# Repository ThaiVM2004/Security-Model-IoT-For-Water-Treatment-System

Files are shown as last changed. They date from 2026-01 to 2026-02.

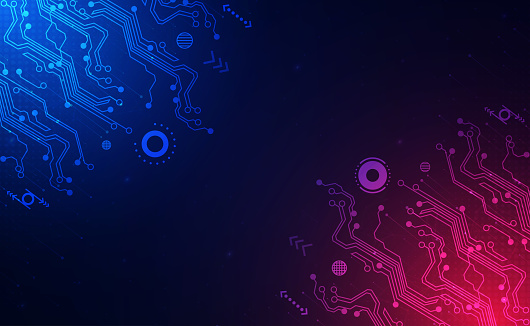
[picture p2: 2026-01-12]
Source/Web Code/superviso-ui/src/Components/Assets/background-4.jpg

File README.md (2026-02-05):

# BUILD A SECURITY MODEL IOT FOR WATER TREATMENT SYSTEM

In this project, I want to build a security model iot, it is applicated in water treatment system.

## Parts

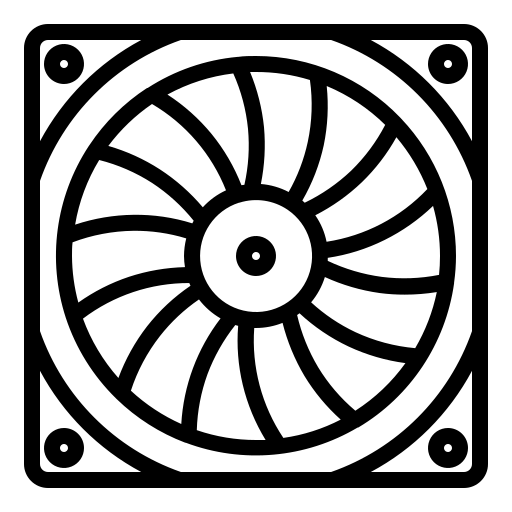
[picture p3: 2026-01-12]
Source/Web Code/superviso-ui/src/Components/Assets/fan-industrial.png

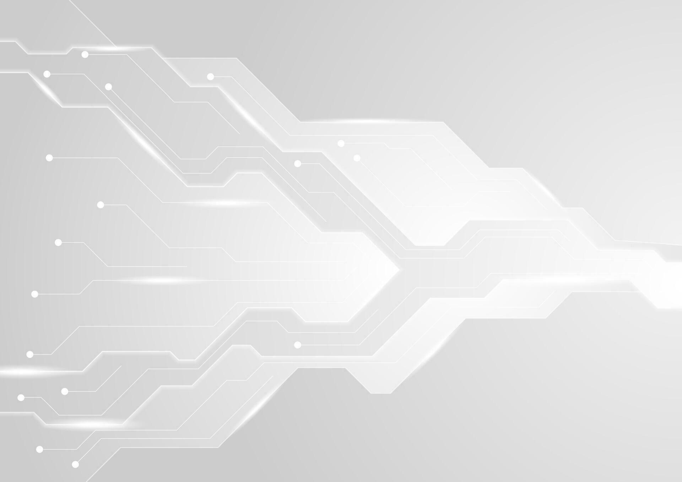
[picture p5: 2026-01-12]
Source/Web Code/superviso-ui/src/Components/Assets/background-3.jpg

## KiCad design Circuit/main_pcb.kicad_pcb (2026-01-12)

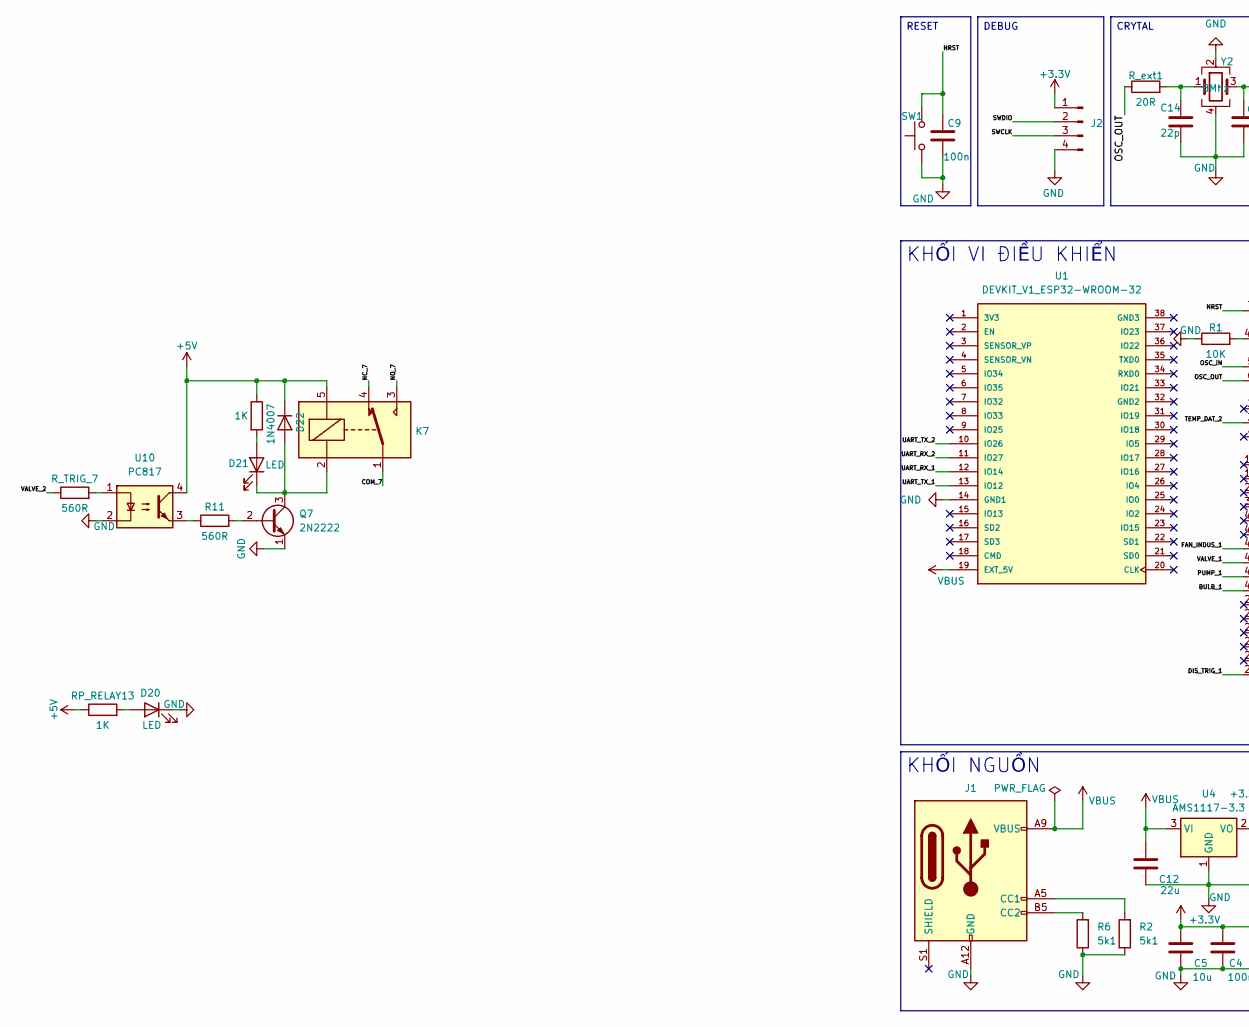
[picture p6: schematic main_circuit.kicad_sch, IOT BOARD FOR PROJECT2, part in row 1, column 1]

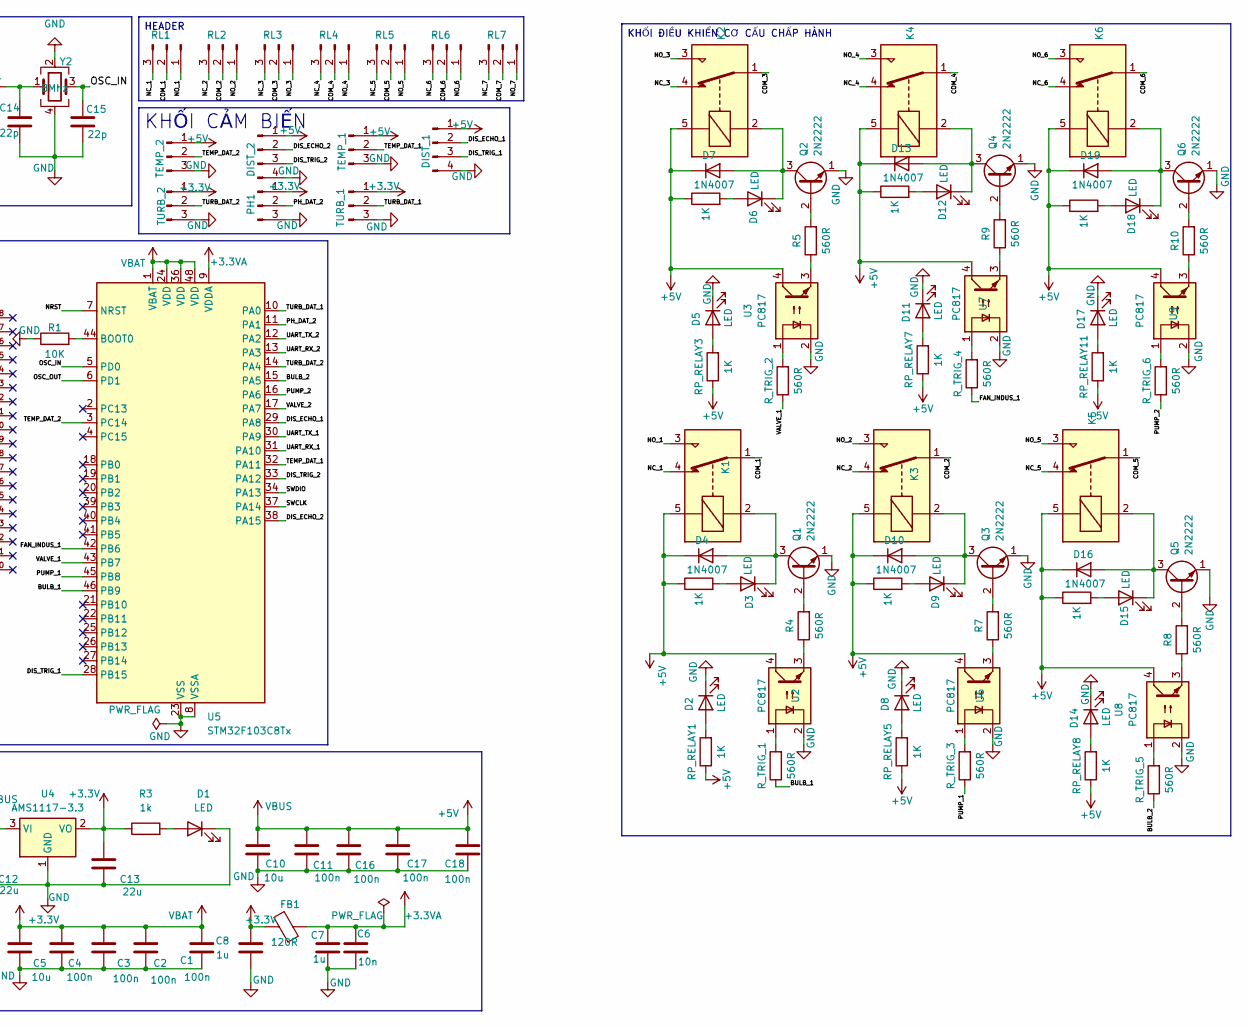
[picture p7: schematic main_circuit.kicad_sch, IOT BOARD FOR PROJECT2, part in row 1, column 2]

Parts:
C1, C2, C3, C4, C9, C11, C16, C17, C18: 100n; C_0805_2012Metric
C5, C10: 10u; C_0805_2012Metric
C6: 10n; C_0805_2012Metric
C7, C8: 1u; C_0805_2012Metric
C12, C13: 22u; C_0805_2012Metric
C14, C15: 22p; C_0603_1608Metric
D1, D2, D3, D5, D6, D8, D9, D11, D12, D14, D15, D17, D18, D20, D21: LED; LED_0805_2012Metric
D4, D7, D10, D13, D16, D19, D22: 1N4007; D_DO-41_SOD81_P10.16mm_Horizontal
DIST_1, DIST_2: Conn_01x04_Pin; PinHeader_1x04_P2.54mm_Vertical
FB1: 120R; L_0805_2012Metric
J1: USB_C_Receptacle_PowerOnly_6P; USB_C_Receptacle_GCT_USB4125-xx-x_6P_TopMnt_Horizontal
J2: ST-LINK; PinHeader_1x04_P2.54mm_Vertical
K1, K2, K3, K4, K5, K6, K7: SANYOU_SRD_Form_C; Relay_SPDT_SANYOU_SRD_Series_Form_C
PH1: Conn_01x03_Pin; PinHeader_1x03_P2.54mm_Vertical
Q1, Q2, Q3, Q4, Q5, Q6, Q7: 2N2222; PinHeader_1x03_P1.27mm_Vertical
R1: 10K; R_0805_2012Metric
R2, R6: 5k1; R_0805_2012Metric
R3: 1k; R_0805_2012Metric
R4, R5, R7, R8, R9, R10, R11: 560R; R_0805_2012Metric
RL1, RL2, RL3, RL4, RL5, RL6, RL7: Conn_01x03_Pin; PinHeader_1x03_P2.54mm_Vertical
RP_RELAY1, RP_RELAY2, RP_RELAY3, RP_RELAY4, RP_RELAY5, RP_RELAY6, RP_RELAY7, RP_RELAY8, RP_RELAY9, RP_RELAY10, RP_RELAY11, RP_RELAY12, RP_RELAY13, RP_RELAY14: 1K; R_0805_2012Metric
R_TRIG_1, R_TRIG_2, R_TRIG_3, R_TRIG_4, R_TRIG_5, R_TRIG_6, R_TRIG_7: 560R; R_0805_2012Metric
R_ext1: 20R; R_0805_2012Metric
SW1: SW_Push; SW_SPST_PTS647_Sx70
TEMP_1, TEMP_2: Conn_01x03_Pin; PinHeader_1x03_P2.54mm_Vertical
TURB_1, TURB_2: Conn_01x03_Pin; PinHeader_1x03_P2.54mm_Vertical
U1: DEVKIT_V1_ESP32-WROOM-32; MODULE_DEVKIT_V1_ESP32-WROOM-32; PARTREV N/A
U2, U3, U6, U7, U8, U9, U10: PC817; DIP-4_W7.62mm
U4: AMS1117-3.3; SOT-223-3_TabPin2
U5: STM32F103C8Tx; LQFP-48_7x7mm_P0.5mm
Y2: 8Mhz; Crystal_SMD_5032-4Pin_5.0x3.2mm

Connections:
+3.3V: C1.1, C2.1, C3.1, C4.1, C5.1, C8.1, C13.1, FB1.2, J2.1, PH1.1, R3.1, TURB_1.1, TURB_2.1, U4.2 (VO), U5.1 (VBAT), U5.24 (VDD), U5.36 (VDD), U5.48 (VDD)
+3.3VA: C6.1, C7.1, FB1.1, U5.9 (VDDA)
+5V: C10.1, C11.1, C12.1, C16.1, C17.1, C18.1, D4.1 (K), D7.1 (K), D10.1 (K), D13.1 (K), D16.1 (K), D19.1 (K), D22.1 (K), DIST_1.1, DIST_2.1, J1.A9 (VBUS), J1.B9 (VBUS), K1.5, K2.5, K3.5, K4.5, K5.5, K6.5, K7.5, RP_RELAY1.1, RP_RELAY2.1, RP_RELAY3.1, RP_RELAY4.1, RP_RELAY5.1, RP_RELAY6.1, RP_RELAY7.1, RP_RELAY8.1, RP_RELAY9.1, RP_RELAY10.1, RP_RELAY11.1, RP_RELAY12.1, RP_RELAY13.1, RP_RELAY14.1, TEMP_1.1, TEMP_2.1, U1.19 (EXT_5V), U2.4, U3.4, U4.3 (VI), U6.4, U7.4, U8.4, U9.4, U10.4
/BULB_1: R_TRIG_1.1, U5.46 (PB9)
/BULB_2: R_TRIG_5.1, U5.15 (PA5)
/COM_1: K1.1, RL1.2
/COM_2: K3.1, RL2.2
/COM_3: K2.1, RL3.2
/COM_4: K4.1, RL4.2
/COM_5: K5.1, RL5.2
/COM_6: K6.1, RL6.2
/COM_7: K7.1, RL7.2
/DIS_ECHO_1: DIST_1.2, U5.29 (PA8)
/DIS_ECHO_2: DIST_2.2, U5.38 (PA15)
/DIS_TRIG_1: DIST_1.3, U5.28 (PB15)
/DIS_TRIG_2: DIST_2.3, U5.33 (PA12)
/FAN_INDUS_1: R_TRIG_4.1, U5.42 (PB6)
/NC_1: K1.4, RL1.3
/NC_2: K3.4, RL2.3
/NC_3: K2.4, RL3.3
/NC_4: K4.4, RL4.3
/NC_5: K5.4, RL5.3
/NC_6: K6.4, RL6.3
/NC_7: K7.4, RL7.3
/NO_1: K1.3, RL1.1
/NO_2: K3.3, RL2.1
/NO_3: K2.3, RL3.1
/NO_4: K4.3, RL4.1
/NO_5: K5.3, RL5.1
/NO_6: K6.3, RL6.1
/NO_7: K7.3, RL7.1
/NRST: C9.1, SW1.2, U5.7 (NRST)
/OSC_IN: C15.1, U5.5 (PD0), Y2.3
/OSC_OUT: R_ext1.1, U5.6 (PD1)
/PH_DAT_2: PH1.2, U5.11 (PA1)
/PUMP_1: R_TRIG_3.1, U5.45 (PB8)
/PUMP_2: R_TRIG_6.1, U5.16 (PA6)
/SWCLK: J2.3, U5.37 (PA14)
/SWDIO: J2.2, U5.34 (PA13)
/TEMP_DAT_1: TEMP_1.2, U5.32 (PA11)
/TEMP_DAT_2: TEMP_2.2, U5.3 (PC14)
/TURB_DAT_1: TURB_1.2, U5.10 (PA0)
/TURB_DAT_2: TURB_2.2, U5.14 (PA4)
/UART_RX_1: U1.12 (IO14), U5.31 (PA10)
/UART_RX_2: U1.11 (IO27), U5.13 (PA3)
/UART_TX_1: U1.13 (IO12), U5.30 (PA9)
/UART_TX_2: U1.10 (IO26), U5.12 (PA2)
/VALVE_1: R_TRIG_2.1, U5.43 (PB7)
/VALVE_2: R_TRIG_7.1, U5.17 (PA7)
GND: C1.2, C2.2, C3.2, C4.2, C5.2, C6.2, C7.2, C8.2, C9.2, C10.2, C11.2, C12.2, C13.2, C14.2, C15.2, C16.2, C17.2, C18.2, D1.1 (K), D2.1 (K), D5.1 (K), D8.1 (K), D11.1 (K), D14.1 (K), D17.1 (K), D20.1 (K), DIST_1.4, DIST_2.4, J1.A12 (GND), J1.B12 (GND), J2.4, PH1.3, Q1.1 (E), Q2.1 (E), Q3.1 (E), Q4.1 (E), Q5.1 (E), Q6.1 (E), Q7.1 (E), R1.1, R2.1, R6.1, SW1.1, TEMP_1.3, TEMP_2.3, TURB_1.3, TURB_2.3, U1.14 (GND1), U2.2, U3.2, U4.1 (GND), U5.8 (VSSA), U5.23 (VSS), U5.35 (VSS), U5.47 (VSS), U6.2, U7.2, U8.2, U9.2, U10.2, Y2.2, Y2.4
unnamed: C14.1, R_ext1.2, Y2.1
unnamed: D1.2 (A), R3.2
unnamed: D2.2 (A), RP_RELAY1.2
unnamed: D3.2 (A), RP_RELAY2.2
unnamed: D3.1 (K), D4.2 (A), K1.2, Q1.3 (C)
unnamed: D5.2 (A), RP_RELAY3.2
unnamed: D6.2 (A), RP_RELAY4.2
unnamed: D6.1 (K), D7.2 (A), K2.2, Q2.3 (C)
unnamed: D8.2 (A), RP_RELAY5.2
unnamed: D9.2 (A), RP_RELAY6.2
unnamed: D9.1 (K), D10.2 (A), K3.2, Q3.3 (C)
unnamed: D11.2 (A), RP_RELAY7.2
unnamed: D12.2 (A), RP_RELAY10.2
unnamed: D12.1 (K), D13.2 (A), K4.2, Q4.3 (C)
unnamed: D14.2 (A), RP_RELAY8.2
unnamed: D15.2 (A), RP_RELAY9.2
unnamed: D15.1 (K), D16.2 (A), K5.2, Q5.3 (C)
unnamed: D17.2 (A), RP_RELAY11.2
unnamed: D18.2 (A), RP_RELAY12.2
unnamed: D18.1 (K), D19.2 (A), K6.2, Q6.3 (C)
unnamed: D20.2 (A), RP_RELAY13.2
unnamed: D21.2 (A), RP_RELAY14.2
unnamed: D21.1 (K), D22.2 (A), K7.2, Q7.3 (C)
unnamed: J1.A5 (CC1), R2.2
unnamed: J1.B5 (CC2), R6.2
unnamed: Q1.2 (B), R4.2
unnamed: Q2.2 (B), R5.2
unnamed: Q3.2 (B), R7.2
unnamed: Q4.2 (B), R9.2
unnamed: Q5.2 (B), R8.2
unnamed: Q6.2 (B), R10.2
unnamed: Q7.2 (B), R11.2
unnamed: R4.1, U2.3
unnamed: R5.1, U3.3
unnamed: R7.1, U6.3
unnamed: R8.1, U8.3
unnamed: R9.1, U7.3
unnamed: R10.1, U9.3
unnamed: R11.1, U10.3
unnamed: R_TRIG_1.2, U2.1
unnamed: R_TRIG_2.2, U3.1
unnamed: R_TRIG_3.2, U6.1
unnamed: R_TRIG_4.2, U7.1
unnamed: R_TRIG_5.2, U8.1
unnamed: R_TRIG_6.2, U9.1
unnamed: R_TRIG_7.2, U10.1
unnamed: R1.2, U5.44 (BOOT0)

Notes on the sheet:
KHỐI ĐIỀU KHIỂN CƠ CẤU CHẤP HÀNH
KHỐI CẢM BIẾN
DEBUG
HEADER
KHỐI NGUỒN
CRYTAL
KHỐI VI ĐIỀU KHIỂN
RESET

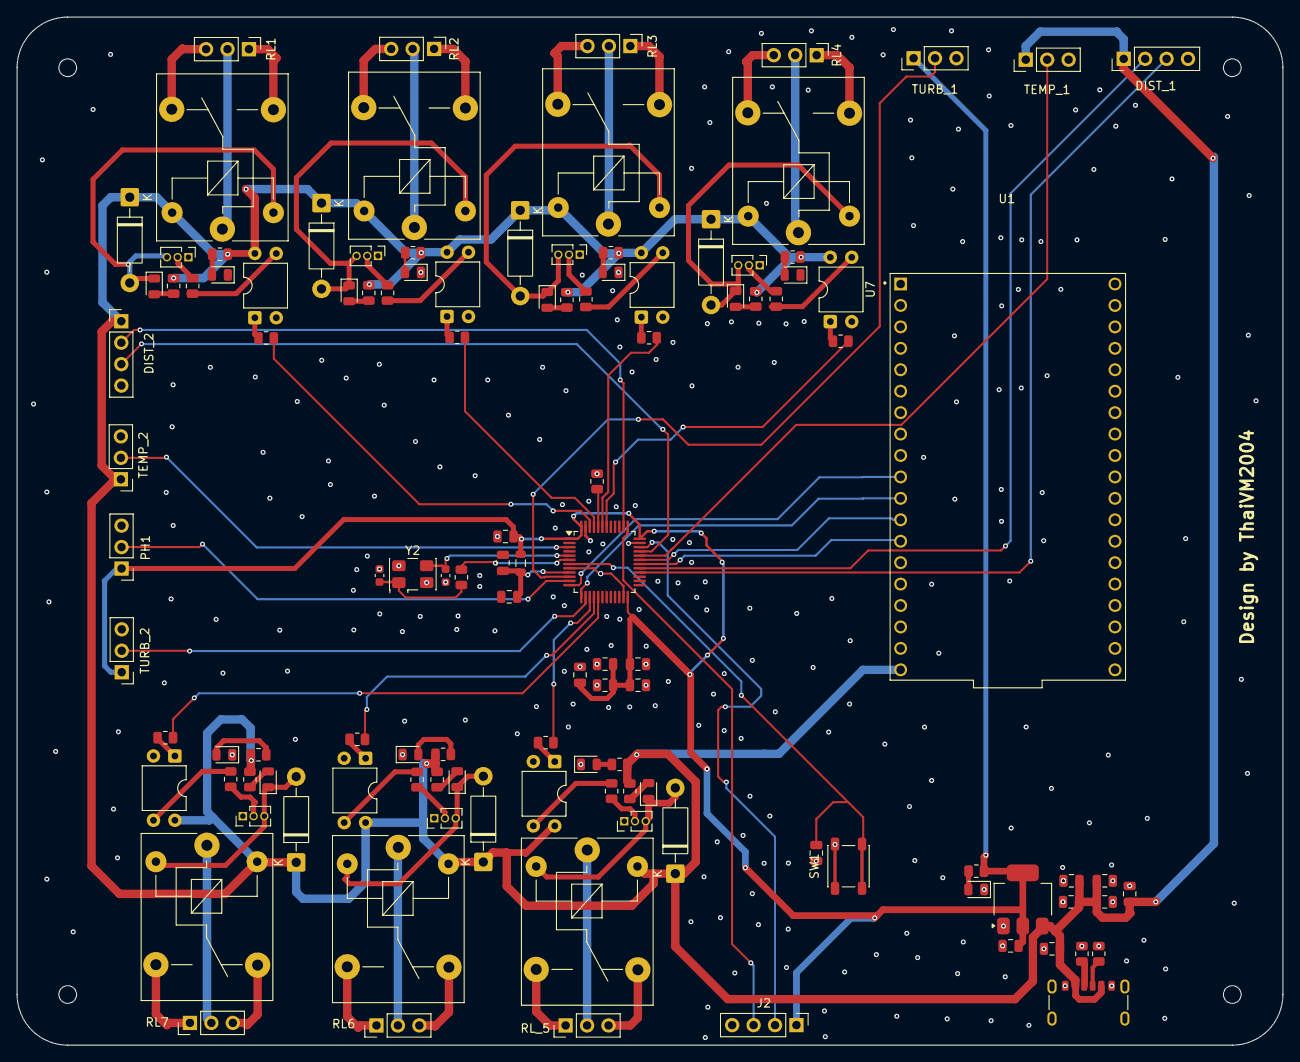
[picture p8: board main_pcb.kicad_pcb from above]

Board: 2 copper layers, 150.0 x 121.8 mm, 120 parts (0 on the bottom side), 97 nets.

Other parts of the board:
H1, H2, H3, H4: MountingHole; MountingHole_2.1mm

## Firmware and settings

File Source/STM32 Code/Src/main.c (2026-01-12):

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
/* Includes ------------------------------------------------------------------*/
#include "main.h"
#include "cmsis_os.h"

/* USER CODE BEGIN Includes */

#include "string.h"
#include "stdio.h"
#include "temp_delay.h"
#include "water_level.h"
#include "turbidity.h"
#include "pH.h"

/* USER CODE END Includes */

/* USER CODE BEGIN PD */

osThreadId_t sensorTask_1_Handle;
osThreadId_t sensorTask_2_Handle;


osMutexId_t uartMutexHandle;
const osMutexAttr_t uartMutex_attributes = {
    .name = "uartMutex"
};

osMutexId_t tempMutex;
osMutexId_t adcMutex;




void StartUartRxTask(void *arg);
void StartSensorTask_1(void *arg);
void StartSensorTask_2(void *arg);

TempSensor_t tempSensor_1;
TempSensor_t tempSensor_2;

HCSR04_t hcsr04_1;
HCSR04_t hcsr04_2;

Turbidity_t turb1;
Turbidity_t turb2;


#define UART_LINE_MAX 64
static uint8_t esp_rx_byte;
static char uart_line_buffer[UART_LINE_MAX];
static uint16_t uart_line_idx = 0;


/* USER CODE END PD */

ADC_HandleTypeDef hadc1;

TIM_HandleTypeDef htim1;
TIM_HandleTypeDef htim2;
TIM_HandleTypeDef htim4;

UART_HandleTypeDef huart1;
UART_HandleTypeDef huart2;

/* Definitions for defaultTask */
osThreadId_t defaultTaskHandle;
const osThreadAttr_t defaultTask_attributes = {
  .name = "defaultTask",
  .stack_size = 128 * 4,
  .priority = (osPriority_t) osPriorityNormal,
};
void SystemClock_Config(void);
static void MX_GPIO_Init(void);
static void MX_USART2_UART_Init(void);
static void MX_TIM1_Init(void);
static void MX_ADC1_Init(void);
static void MX_USART1_UART_Init(void);
static void MX_TIM4_Init(void);
static void MX_TIM2_Init(void);
void StartDefaultTask(void *argument);

/* USER CODE BEGIN 0 */
void HAL_TIM_IC_CaptureCallback(TIM_HandleTypeDef *htim)
{
    if (htim->Instance == TIM1)
    {
        HCSR04_TIM_IC_Callback(&hcsr04_1, htim);
    }
    else if (htim->Instance == TIM2)
    {
        HCSR04_TIM_IC_Callback(&hcsr04_2, htim);
    }
}
void control_device(const char *name, uint8_t state)
{
    GPIO_PinState pinState = (state ? GPIO_PIN_SET : GPIO_PIN_RESET);

    if (strcmp(name, "bulb1") == 0)
        HAL_GPIO_WritePin(GPIOB, GPIO_PIN_9, pinState);

    else if (strcmp(name, "pump1") == 0)
        HAL_GPIO_WritePin(GPIOB, GPIO_PIN_8, pinState);

    else if (strcmp(name, "valve1") == 0)
        HAL_GPIO_WritePin(GPIOB, GPIO_PIN_7, pinState);
    else if (strcmp(name, "fan_industrial1") == 0)
        HAL_GPIO_WritePin(GPIOB, GPIO_PIN_6, pinState);
    else if (strcmp(name, "bulb2") == 0)
        HAL_GPIO_WritePin(GPIOA, GPIO_PIN_5, pinState);
    else if (strcmp(name, "pump2") == 0)
        HAL_GPIO_WritePin(GPIOA, GPIO_PIN_6, pinState);
    else if (strcmp(name, "valve2") == 0)
        HAL_GPIO_WritePin(GPIOA, GPIO_PIN_7, pinState);
    else if (strcmp(name, "fan_industrial2") == 0)
        HAL_GPIO_WritePin(GPIOB, GPIO_PIN_0, pinState);

    else
        return;
}

void StartSensorTask_1(void *arg)

{




    for (;;)
    {
    	HCSR04_Trigger(&hcsr04_1);
        HAL_GPIO_TogglePin(GPIOC, GPIO_PIN_13);

        // Đọc nhiệt độ với mutex
        osMutexAcquire(tempMutex, osWaitForever);
        float temp1 = Temp_Read(&tempSensor_1);
        osMutexRelease(tempMutex);

        // Đọc water level
        uint32_t water = HCSR04_GetDistance(&hcsr04_1);

        // Đọc TDS với mutex
        osMutexAcquire(adcMutex, osWaitForever);
        float tds = TURBIDITY_Read(&turb1);
        osMutexRelease(adcMutex);

        // Gửi UART
        char msg[128];
        int len = snprintf(msg, sizeof(msg),
                           "SENSOR1:TEMP:%.2f;WATER:%lu;TDS:%.2f;PH:%.2f\r\n",
                           temp1, water, tds, 0.0f);

        osMutexAcquire(uartMutexHandle, osWaitForever);
        HAL_UART_Transmit(&huart1, (uint8_t *)msg, len, 1000);
        osMutexRelease(uartMutexHandle);

//        HCSR04_Trigger(&hcsr04_1);
        osDelay(2000);
    }
}

void StartSensorTask_2(void *arg)
{


    for (;;)
    {
        HCSR04_Trigger(&hcsr04_2);
        osMutexAcquire(tempMutex, osWaitForever);
        float temp2 = Temp_Read(&tempSensor_2);
        osMutexRelease(tempMutex);

        // Đọc water level
        uint32_t water2 = HCSR04_GetDistance(&hcsr04_2);

        // Đọc TDS và pH với mutex
        osMutexAcquire(adcMutex, osWaitForever);
        float tds2 = TURBIDITY_Read(&turb2)*10;
        float ph = PH_ReadValue();
        osMutexRelease(adcMutex);

        // Gửi UART
        char msg[128];
        int len = snprintf(msg, sizeof(msg),
                           "SENSOR2:TEMP:%.2f;WATER:%lu;TDS:%.2f;PH:%.2f\r\n",
                           temp2, water2, tds2, ph);

        osMutexAcquire(uartMutexHandle, osWaitForever);
        HAL_UART_Transmit(&huart1, (uint8_t *)msg, len, 1000);
        osMutexRelease(uartMutexHandle);

//        HCSR04_Trigger(&hcsr04_2);
        osDelay(2000);
    }
}


void process_uart2_cmd(char *line)
{
    if (line == NULL) return;

    /* command expected: device/action   e.g. pump1/on or pump1/off */
    char *device = strtok(line, "/");
    char *action = strtok(NULL, "/");

    if (!device || !action) return;

    if (strcmp(action, "on") == 0)
        control_device(device, 1);
    else
        control_device(device, 0);

}

void HAL_UART_RxCpltCallback(UART_HandleTypeDef *huart)
{
    if (huart->Instance == USART2)
    {
        char c = (char)esp_rx_byte;

        if (c != '\n' && c != '\r')
        {
            uart_line_buffer[uart_line_idx++] = c;
            if (uart_line_idx >= UART_LINE_MAX)
                uart_line_idx = 0;
        }
        else
        {
            uart_line_buffer[uart_line_idx] = '\0';

            process_uart2_cmd(uart_line_buffer);

            uart_line_idx = 0;
        }

        HAL_UART_Receive_IT(&huart2, &esp_rx_byte, 1);
    }
}
/* USER CODE END 0 */

/**
  * @brief  The application entry point.
  * @retval int
  */
int main(void)
{

  /* MCU Configuration--------------------------------------------------------*/

  /* Reset of all peripherals, Initializes the Flash interface and the Systick. */
  HAL_Init();

  /* Configure the system clock */
  SystemClock_Config();

  /* Initialize all configured peripherals */
  MX_GPIO_Init();
  MX_USART2_UART_Init();
  MX_TIM1_Init();
  MX_ADC1_Init();
  MX_USART1_UART_Init();
  MX_TIM4_Init();
  MX_TIM2_Init();
  /* USER CODE BEGIN 2 */
  //INIT FUNCTION
  //Cam bien muc nuoc
  HCSR04_Init(&hcsr04_1, &htim1, TIM_CHANNEL_1, GPIOB, GPIO_PIN_15);
  HCSR04_Init(&hcsr04_2, &htim2, TIM_CHANNEL_1, GPIOA, GPIO_PIN_12);
  //Dieu khien GPIO
  HAL_UART_Receive_IT(&huart2, &esp_rx_byte, 1);
  //Ngat de do xung cam bien muc nuoc
  HAL_TIM_IC_Start_IT(&htim1, TIM_CHANNEL_1);
  HAL_TIM_IC_Start_IT(&htim2, TIM_CHANNEL_1);
  //Cam bien nhiet do
  HAL_TIM_Base_Start(&htim4);
  Temp_Init(&tempSensor_1, &htim4, GPIOA, GPIO_PIN_11);
  Temp_Init(&tempSensor_2, &htim4, GPIOC, GPIO_PIN_14);
  //Cam bien pH
  PH_AttachADC(&hadc1, ADC_CHANNEL_1);
  PH_InitFromTwoPoints(0.392f, 2.5f,
		  	  	  	  1.54f, 10.5f);
  //Cam bien do duc
  TURBIDITY_Init(&turb1, &hadc1, ADC_CHANNEL_0);  // sensor 1
  TURBIDITY_Init(&turb2, &hadc1, ADC_CHANNEL_4);  // sensor 2



  /* USER CODE END 2 */

  /* Init scheduler */
  osKernelInitialize();

  /* USER CODE BEGIN RTOS_MUTEX */
  /* add mutexes, ... */
  uartMutexHandle = osMutexNew(&uartMutex_attributes);
  const osMutexAttr_t adcMutex_attr = { .name = "adcMutex" };
  const osMutexAttr_t tempMutex_attr = { .name = "tempMutex" };
  adcMutex = osMutexNew(&adcMutex_attr);
  tempMutex = osMutexNew(&tempMutex_attr);

  if (uartMutexHandle == NULL || adcMutex == NULL || tempMutex == NULL)
  {
      Error_Handler();
  }
  /* USER CODE END RTOS_MUTEX */

  /* USER CODE BEGIN RTOS_SEMAPHORES */
  /* add semaphores, ... */
  /* USER CODE END RTOS_SEMAPHORES */

  /* USER CODE BEGIN RTOS_TIMERS */
  /* start timers, add new ones, ... */
  /* USER CODE END RTOS_TIMERS */

  /* USER CODE BEGIN RTOS_QUEUES */
  /* add queues, ... */
  /* USER CODE END RTOS_QUEUES */

  /* Create the thread(s) */
  /* creation of defaultTask */
  defaultTaskHandle = osThreadNew(StartDefaultTask, NULL, &defaultTask_attributes);

  /* USER CODE BEGIN RTOS_THREADS */
  /* add threads, ... */


  const osThreadAttr_t sensor_1_Attr = {
      .name = "SENSOR_1",
      .priority = osPriorityHigh,
      .stack_size = 2048
  };
  const osThreadAttr_t sensor_2_Attr = {
      .name = "SENSOR_2",
      .priority = osPriorityNormal,
      .stack_size = 2048
  };


   sensorTask_1_Handle = osThreadNew(StartSensorTask_1, NULL, &sensor_1_Attr);
   sensorTask_2_Handle = osThreadNew(StartSensorTask_2, NULL, &sensor_2_Attr);





//  uartRxTaskHandle = osThreadNew(StartUartRxTask, NULL, &uartAttr);

  /* USER CODE END RTOS_THREADS */

  /* USER CODE BEGIN RTOS_EVENTS */
  /* add events, ... */
  /* USER CODE END RTOS_EVENTS */

  /* Start scheduler */
  osKernelStart();

  /* We should never get here as control is now taken by the scheduler */

  /* Infinite loop */
  /* USER CODE BEGIN WHILE */
  while (1)
  {
    /* USER CODE END WHILE */

    /* USER CODE BEGIN 3 */
  }
  /* USER CODE END 3 */
}

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
/* USER CODE BEGIN Header_StartDefaultTask */
/**
  * @brief  Function implementing the defaultTask thread.
  * @param  argument: Not used
  * @retval None
  */
/* USER CODE END Header_StartDefaultTask */
void StartDefaultTask(void *argument)
{
  /* USER CODE BEGIN 5 */
  /* Infinite loop */
  for(;;)
  {
    osDelay(1);
  }
  /* USER CODE END 5 */
}

/**
  * @brief  This function is executed in case of error occurrence.
  * @retval None
  */
void Error_Handler(void)
{
  /* USER CODE BEGIN Error_Handler_Debug */
  /* User can add his own implementation to report the HAL error return state */
  __disable_irq();
  while (1)
  {
  }
  /* USER CODE END Error_Handler_Debug */
}

#ifdef  USE_FULL_ASSERT
/**
  * @brief  Reports the name of the source file and the source line number
  *         where the assert_param error has occurred.
  * @param  file: pointer to the source file name
  * @param  line: assert_param error line source number
  * @retval None
  */
void assert_failed(uint8_t *file, uint32_t line)
{
  /* USER CODE BEGIN 6 */
  /* User can add his own implementation to report the file name and line number,
     ex: printf("Wrong parameters value: file %s on line %d\r\n", file, line) */
  /* USER CODE END 6 */
}
#endif /* USE_FULL_ASSERT */

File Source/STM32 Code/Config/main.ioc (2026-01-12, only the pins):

Mcu.UserName=STM32F103C8Tx
PA0-WKUP.Signal=ADCx_IN0
PA1.Signal=ADCx_IN1
PA10.Signal=USART1_RX
PA11.Signal=GPIO_Output
PA12.Signal=GPIO_Output
PA15.Signal=S_TIM2_CH1_ETR
PA2.Signal=USART2_TX
PA3.Signal=USART2_RX
PA4.Signal=ADCx_IN4
PA5.Signal=GPIO_Output
PA6.Signal=GPIO_Output
PA7.Signal=GPIO_Output
PA8.Signal=S_TIM1_CH1
PA9.Signal=USART1_TX
PB0.Signal=GPIO_Output
PB15.Signal=GPIO_Output
PB6.Signal=GPIO_Output
PB7.Signal=GPIO_Output
PB8.Signal=GPIO_Output
PB9.Signal=GPIO_Output
PC13-TAMPER-RTC.Signal=GPIO_Output
PC14-OSC32_IN.Signal=GPIO_Output
PD0-OSC_IN.Signal=RCC_OSC_IN
PD1-OSC_OUT.Signal=RCC_OSC_OUT

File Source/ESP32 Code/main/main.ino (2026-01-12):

#include <WiFi.h>
#include <PubSubClient.h>
#include <ArduinoJson.h>


const char* ssid = "HOBAHOME TRET2";
const char* password = "12345678";
const char* mqtt_server = "192.168.1.115";
const int   mqtt_port  = 1883;

const char* mqtt_sub_topic   = "iot/control";
const char* mqtt_pub_sensor1 = "iot/sensor1";
const char* mqtt_pub_sensor2 = "iot/sensor2";

WiFiClient espClient;
PubSubClient client(espClient);


HardwareSerial UART_CMD(2);

HardwareSerial UART_SENSOR(1);

String uartSensorBuffer = "";

int mapWaterLevel(int distanceCm)
{

    
    const int EMPTY_DISTANCE = 12.5;  
    const int FULL_DISTANCE  = 1;   
    

    if (distanceCm >= EMPTY_DISTANCE) return 0;
    if (distanceCm <= FULL_DISTANCE)  return 100;
    
    int percentage = map(distanceCm, EMPTY_DISTANCE, FULL_DISTANCE, 0, 100);
    
    if (percentage < 0)   percentage = 0;
    if (percentage > 100) percentage = 100;
    
    return percentage;
}

void callback(char* topic, byte* payload, unsigned int length)
{
    StaticJsonDocument<256> doc;
    if (deserializeJson(doc, payload, length)) return;

    const char* device = doc["device"];
    const char* action = doc["action"];
    if (!device || !action) return;

    char cmd[64];
    snprintf(cmd, sizeof(cmd), "%s/%s\n", device, action);

    Serial.print("TX → STM32 (UART2): ");
    Serial.print(cmd);

    UART_CMD.print(cmd);
}

void reconnect()
{
    while (!client.connected())
    {
        Serial.print("MQTT connecting... ");

        if (client.connect("ESP32-UART-HUB"))
        {
            Serial.println("OK");
            client.subscribe(mqtt_sub_topic);
        }
        else
        {
            Serial.print("Failed, rc=");
            Serial.println(client.state());
            delay(2000);
        }
    }
}

void publishSensorData(String raw)
{
    StaticJsonDocument<256> doc;

    if (raw.startsWith("SENSOR1:"))
    {
        float temp = 0;
        int   waterRaw = 0;  
        float tds  = 0;

        int t1 = raw.indexOf("TEMP:");
        int t2 = raw.indexOf(";WATER:");
        int t3 = raw.indexOf(";TDS:");

        if (t1 < 0 || t2 < 0 || t3 < 0) return;

        temp     = raw.substring(t1 + 5, t2).toFloat();
        waterRaw = raw.substring(t2 + 7, t3).toInt();
        tds      = raw.substring(t3 + 5).toFloat();

  
        int waterPercent = mapWaterLevel(waterRaw);

        doc["temp"]  = temp;
        doc["water"] = waterPercent;  
        doc["tds"]   = tds;

        char jsonOut[128];
        serializeJson(doc, jsonOut);

        Serial.print("MQTT publish → SENSOR1:");
        Serial.println(jsonOut);

        client.publish(mqtt_pub_sensor1, jsonOut);
        return;
    }

    if (raw.startsWith("SENSOR2:"))
    {
        float temp = 0;
        int   waterRaw = 0;  
        float tds  = 0;
        float ph   = 0;

        int t1 = raw.indexOf("TEMP:");
        int t2 = raw.indexOf(";WATER:");
        int t3 = raw.indexOf(";TDS:");
        int t4 = raw.indexOf(";PH:");

        if (t1 < 0 || t2 < 0 || t3 < 0 || t4 < 0) return;

        temp     = raw.substring(t1 + 5, t2).toFloat();
        waterRaw = raw.substring(t2 + 7, t3).toInt();
        tds      = raw.substring(t3 + 5, t4).toFloat();
        ph       = raw.substring(t4 + 4).toFloat();


        int waterPercent = mapWaterLevel(waterRaw);

        doc["temp"]  = temp;
        doc["water"] = waterPercent;  
        doc["tds"]   = tds;
        doc["ph"]    = ph;

        char jsonOut[128];
        serializeJson(doc, jsonOut);

        Serial.print("MQTT publish → SENSOR2:");
        Serial.println(jsonOut);

        client.publish(mqtt_pub_sensor2, jsonOut);
        return;
    }
}


void setup()
{
    Serial.begin(115200);

    
    UART_CMD.begin(115200, SERIAL_8N1, 26, 27); 
    Serial.println("UART2 Ready (Commands → STM32)");

   
    UART_SENSOR.begin(9600, SERIAL_8N1, 12, 14);
    Serial.println("UART1 Ready (Sensor from STM32)");

    
    Serial.print("WiFi connecting...");
    WiFi.begin(ssid, password);

    while (WiFi.status() != WL_CONNECTED)
    {
        Serial.print(".");
        delay(300);
    }
    Serial.println("\nWiFi OK");

    
    client.setServer(mqtt_server, mqtt_port);
    client.setCallback(callback);
    reconnect();
}


void loop()
{
    if (!client.connected()) reconnect();
    client.loop();

    
    while (UART_SENSOR.available())
    {
        char c = UART_SENSOR.read();

        if (c == '\n' || c == '\r')
        {
            if (uartSensorBuffer.length() > 0)
            {
                Serial.print("STM32 UART1 → ");
                Serial.println(uartSensorBuffer);

                publishSensorData(uartSensorBuffer);

                uartSensorBuffer = "";
            }
        }
        else
        {
            if (uartSensorBuffer.length() < 256)
                uartSensorBuffer += c;
        }
    }
}

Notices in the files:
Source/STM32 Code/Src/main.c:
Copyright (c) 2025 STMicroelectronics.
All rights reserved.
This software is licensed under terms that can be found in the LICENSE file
